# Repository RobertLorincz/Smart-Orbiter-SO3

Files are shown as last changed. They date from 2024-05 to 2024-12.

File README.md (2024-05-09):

# Smart-Orbiter-SO3
This brand new all in one extruder design with many cool features we call Smart Orbiter v3.0  is one of my latest and finest extruder design made in collaboration with LDO Motors. The extrusion system concept and mechanical performances are similar to the Orbiter v2.0 but completely redesigned from scratch.

SO3

**Summary of the coolest features:**

- Pure plated copper heat-block with 72W ceramic heater and Bontech CHT nozzle for highest possible weight VS flow ratio;

- Heat-break performance optimized with finite elements analysis for extreme temperature gradient to ensure clogless free printing experience;

- Unique tensioning mechanism with elastic predefined tension levels

- Frameless recessed 24V fan to reduce the extruder weight and outside dimension

- Large RNC coated dual drive gears with planetary gear reduction, similar to orbiter v2.0

- New precision main shaft design to reduce gear eccentricity

- Full aluminum housing with Delrin plastic gears for low noise and long lifetime

- The smart feature – integrated electronics

- Easy remove system of the secondary drive gear for easy cleaning and maintenance

- Double filament exit guide system for best TPU printing performance

- Overall weight is 175g

**SO3 specifications:**

- Drive type: 12mm dual drive extrusion system

- Weight: 175g including standard hotend

- Nominal steps / mm (16x micro stepping): 690

- Rotation distance: 4.69

- Extrusion force: 6.5Kg+

- Gear ratio: 7.5:1

- Max stepper current: 0.85A RMS (1.2A peak), derating over 50°C ambient temperature.

- Min stepper current: 0.55A RMS (0.75A peak) for operation up to 70°C ambient temperature

- Heater temperature sensor type: ATC Semitec 104NT-4-R025H42G

- Extruder fan: 24V frameless fan with speed signal

- Maximum operating temperature: 90°C (with motor current derating down to 0.55A RMS)

- Filament sensing

- Filament unload

- Hotend lit

- Filament input lit – RGB LED WS2812B type

- Extruder temperature senor: 100K NTC Generic 3950

- Smart features supply: 3.3V or 5V

For more details please visit: https://www.orbiterprojects.com/so3/

Join our support group on Facebook: https://www.facebook.com/groups/705637896767655

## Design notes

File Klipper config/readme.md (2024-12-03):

Changes v2.2.6
- print cancel restores the printer idle timer to 10 min

Changes v2.2.5

- Included CANCEL macro for user using the sensor macros instead of their own macros
- Pausing printer due to runnout detection increases printer timeout to 3600s - 1h (configurable by pause_timeout); timeout set back to default ten minutes after print resume.
- improved temperature restore behavior
- Filament automatic unload after runnout can be disabled by variable disable_runout_unload.
- corrected some minor bugs and spelling
- messages sent to console show SO3: prefix
- corrected RGB led incorrect color status for some failure cases

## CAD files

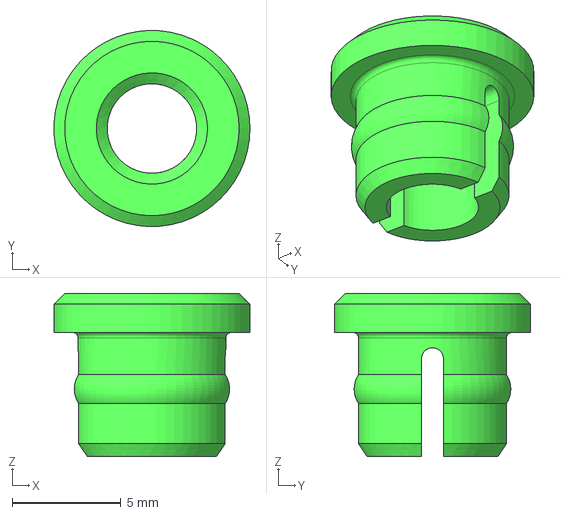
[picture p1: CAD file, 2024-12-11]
3D CAD/SO3_LightRing.step
8.99 x 9.00 x 7.50 mm

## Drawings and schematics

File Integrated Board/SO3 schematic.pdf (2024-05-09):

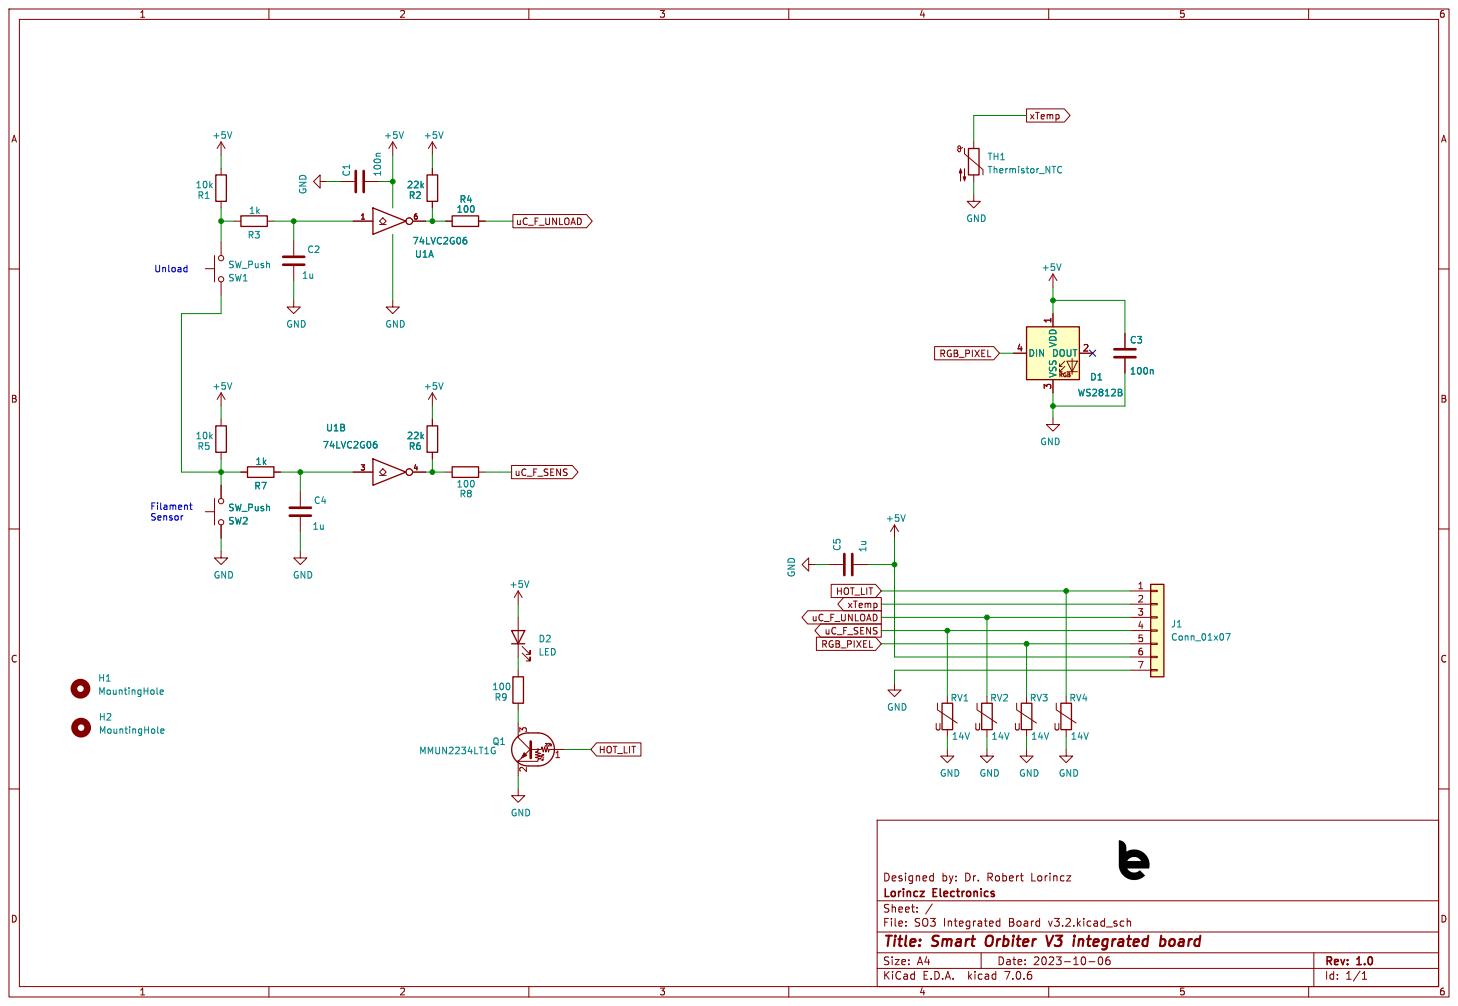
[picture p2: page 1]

Id: 1/1 Title: Smart Orbiter V3 integrated board

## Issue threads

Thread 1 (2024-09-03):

Spare parts?

jjl40, 2024-09-03:
The wires for the hotend cooling fan are too short to reach the tool board and are likely to get pinched. If the wires were 10 mm longer it would be much easier to install. The next problem is finding a replacement.

RobertLorincz, 2024-09-08:
What is the length of your wire, in my case, I had not really issues, but could it be that yours came shorter?

RobertLorincz, 2024-09-08:
For spare parts, you need to ask your local supplier, I insisted a lot on having spare parts also available, but for some reason vendors are not open to it. Its a real issue, I admit, but unfortunately it's hard on my side to change this. It would be better if customers complained directly to the vendors because they can order replacement parts from LDO...but they are not willing to right now. I even asked to at least provide spare parts via AliExpress...so far, still no parts there. Fabreko and Filastruder has some in the US but that is not convenient for everybody.

jjl40, 2024-09-08:
Thank you for your prompt reply Robert,

The hotend fan wire is ~120mm. My mount is a bit unusual due to its layout. I fixed the problem by creating a conduit in the mount so the wire has a direct route to the toolboard. [image0.jpeg]

The only other issue I have is that I have not found a description of how to use the filament load/change. Everything is working fine (the assembly and installation is well documented) but I have not used the automatic loading/change feature.

Cheers

John Lytle

On Sep 8, 2024, at 5:12 AM, LorinczElectronics ***@***.***> wrote:

What is the length of your wire, in my case, I had not really issues, but could it be that yours came shorter?

—
Reply to this email directly, view it on GitHub<https://github.com/RobertLorincz/Smart-Orbiter-SO3/issues/1#issuecomment-2336609975>, or unsubscribe<https://github.com/notifications/unsubscribe-auth/AIE3KPQIGSDHM2OEWTE6K4TZVQIG5AVCNFSM6AAAAABNRGKOSWVHI2DSMVQWIX3LMV43OSLTON2WKQ3PNVWWK3TUHMZDGMZWGYYDSOJXGU>.
You are receiving this because you authored the thread.Message ID: ***@***.***>

jjl40, 2024-09-08:
Thanks again Robert,

I contacted KB3D, where I purchased my Orbiter 3, and Kris informed me that he has the fans in stock. The website was not updated at that time.
This is very convenient for me as KB3D is a short drive for me, just up the road in Twinsburg, Ohio.

Cheers

John Lytle

On Sep 8, 2024, at 5:16 AM, LorinczElectronics ***@***.***> wrote:

For spare parts, you need to ask your local supplier, I insisted a lot on having spare parts also available, but for some reason vendors are not open to it. Its a real issue, I admit, but unfortunately it's hard on my side to change this. It would be better if customers complained directly to the vendors because they can order replacement parts from LDO...but they are not willing to right now. I even asked to at least provide spare parts via AliExpress...so far, still no parts there. Fabreko and Filastruder has some in the US but that is not convenient for everybody.

—
Reply to this email directly, view it on GitHub<https://github.com/RobertLorincz/Smart-Orbiter-SO3/issues/1#issuecomment-2336611208>, or unsubscribe<https://github.com/notifications/unsubscribe-auth/AIE3KPXBTTXBOMIJBFYKJKLZVQIV3AVCNFSM6AAAAABNRGKOSWVHI2DSMVQWIX3LMV43OSLTON2WKQ3PNVWWK3TUHMZDGMZWGYYTCMRQHA>.
You are receiving this because you authored the thread.Message ID: ***@***.***>

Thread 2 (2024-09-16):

revo vs non-revo

mindforger, 2024-09-16:
I have no idea what the difference between the revo and non-revo version is, in the model the only difference seems to be the cableing of the heater, can someone explain? because shop sites also do not state the difference clearly only a 20ish dollar difference

CarVac, 2024-09-23:
Revo versions are for the E3D Revo quick-swap integrated-heatbreak nozzles, not v6 nozzles.

I'd expect that the heatbreak connection is different, the heater is going to be a revo heater of some sort (what wattage?), and there'd be some sort of attachment point for the heater's spring.

mindforger, 2024-09-23:
thank you, i did not visit the site, i was browsing github for extruder options since i wanted to build my own head for my sv08 ... unfortunately i already ruled out the orbiter v3.0 becasue it is too wide to replace the original head and i was unsure if i could use it with the trianglelabs chc pro ... it was a bit confusing to only see the difference in the 3d file

Closed 2024-09-23.

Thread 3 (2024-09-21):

Wire colors in SO3.cfg are backwards

CarVac, 2024-09-21:
I tried to wire my SO3 based on the config file but was getting nonsensical results.

I checked for the thermistor and realized that all the SO3 integrated board wires had backwards colors.

Here's my findings:

```
Orange: ground
White:  5v
Gray:   RGB
Brown:  filament sensor
Yellow: unload button
Red:    temperature
Blue:   hotend light
```

Thus the aliases code should be:

```
  filament_sensor_pin = PC7,         # BROWN signal shall be connected to a digital I/O pin
  filament_unload_pin = PC6,         # YELLOW signal shall be connected to a digital I/O pin
  RGB_pin = PG8,                     # GRAY signal shall be connected to a digital I/O pin
  extruder_temperature_pin = PC1,    # RED signal shall be connected to a temperature sensing input pin
  hotend_lit_pin = PA1,              # BLUE signal shall be connected to a digital I/O pin
```

Also the colors should be documented somewhere else. Maybe on the schematic.

nico9889, 2024-09-21:
I can confirm the issue on the Revo version of the Smart Orbiter, I was convinced the IC board was faulty but after trying @CarVac's color coding I was able to lit the NeoPixel using an Arduino (I still need to test everything else since I need to crimp again all the connectors... and explain to the vendor that the board is probably magically working again and I don't need a replacement anymore 🙈).

@RobertLorincz I'd suggest to create a dedicated page with instructions to setup the Smart Orbiter, I completely missed the reference image under the point "3.3 Integrated Smart Features" in the current page (https://www.orbiterprojects.com/so3/) since it contains **a lot** of mixed information and I didn't expect to find wiring related information under the "Firmware configuration" section.

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

I think the image in the current page is fine, but it need to be put in a more evident place. I wouldn't rely on the cable colors unless there's some kind of warranty that they won't change in the future (I.E: due to a manufacturer decision).

CarVac, 2024-09-21:
Huh, I didn't register that image at all.

Maybe you're right, it probably shouldn't specify wire colors in case it changes.

But I'm glad my findings were able to help someone. Now to wait for my replacement hotend to come in... I had a DOA CHC.

nico9889, 2024-09-21:
I created a pull request to fix the colors specified in the configuration and I added more instruction to wire the Smart Orbiter as well to avoid any possible future mistake. I took the liberty to add you as a co-author since you found both the error and the right wire colors.

RobertLorincz, 2024-09-23:
The problem is that the supplier mixed up the colors and there is not only one variant out there. So I prefer people follows the pin numberings and definition instead of the wire colors.

nico9889, 2024-09-23:
That's exactly what I was worried about. I don't know how familiar you are with GitHub, but I opened a pull request #4 to update the comments in the configuration. I changed the colors according to what CarVac reported and added the pin numbering on the top. Should I remove the colors? Is it fine for you to have the pin numbering inside the configuration? Do you prefer updating the configuration by yourself instead?

If you'll find some time to do that, I'd still strongly suggest to create a dedicated web page with the instruction to setup the Smart Orbiter 3, it's easy to miss the image with the pin numbering on the current page. As a side note I need to make you notice that the website is completely missing information about the Revo version (aside from the small paragraph in the blog post about the SO3), so some people are getting confused #2.

The configuration need to be updated for sure since it's misleading, but about the website it's just a my opinion.

CarVac, 2024-09-23:
I would want to remove all references to colors in the configuration, then, and just have a physical order description in the file.

nico9889, 2024-09-23:
I agree, but I’ll wait for RobertLorincz final decision since this is it’s own project.

Closed 2025-01-16.

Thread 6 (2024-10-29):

E3D PZ Probe

tamebits, 2024-10-29:
Although from the outside it looks as if there was no way to do it, I wanted to double check if there is a way to mount an [E3D PZ Probe](https://e3d-online.com/blogs/news/introducing-pz-probe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) into SO3? This would be an awesome combination.

But it looks like the heat sink is fully integrated into the extruder body.

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

RobertLorincz, 2024-10-30:
In the way this design is done, its not possible to implement it into the SO3...

Tomblarom, 2024-11-29:
I'm using SO3 in combo with a Cartographer3D. I made a neat design, so that it's integrated in the fan and [posted about it here](https://www.facebook.com/groups/705637896767655/posts/1387416425256462).

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

For Cartographer3D there is a new mode called [Survey Touch](https://docs.cartographer3d.com/cartographer-probe/classic-vs-survey-touch). It uses the electrial interference, to detect whether the nozzle touched the bed, functionwise very similar to the E3D PZ Probe. Sure it is not as neatly integrated, but still one of the most precise probes that are available right now.

RobertLorincz, 2024-11-29:
nice design.

tamebits, 2024-11-30:
I’m currently working on a similar solution for beacon probe. I’m still thinking about leaving it in der carrier so I don’t need one for each tool head.

Closed 2024-11-30.

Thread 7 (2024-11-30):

Friction in the upper filament path

tamebits, 2024-11-30:
I just received my SO3. It feels like there is too much friction in the first section. The force required to get the filament moving is somewhere in the range of 7-10 N.
I see something in the filament path. I guess it is some actuator for a micro switch that serves as a filament runout sensor.

Is this amount of friction normal?

RobertLorincz, 2024-12-01:
No, it's not normal; the filament should go in pretty easily. Please take the extruder apart and check if there is not some debris inside the extruder. ALso check the position of the internal electronics board; it could be that the board is not in the correct place and it is closer to the filament than it should be.

tamebits, 2024-12-01:
I took it apart and did not find any debris. I checked the filament diameter and it is 1.75 mm.
The internal board sits flush on the aluminium part. SW2 sits flush on the PCB.
PCB + SW2 fully compressed is 5mm thick. PCB + SW2 released ~ 5.5 mm
The actuator ball is 4 mm.
Anything wrong with that?

The ball left an indent in the switch's button. Looks like the switch is being "over-actuated" which results a lot of friction.

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

RobertLorincz, 2024-12-03:
I can confirm the issue; I'm trying to find out which component is out of spek. It seems there is an issue with some parts causing this issue, I'm in contact with LDO to find and correct the issue. Sure, you will receive replacement parts to fix this.

tamebits, 2024-12-14:
Any update?

tamebits, 2024-12-19:
Thank you Robert,

I asked LDO to get in touch with me. Looks like I have to find another project for the holidays. Or maybe I'll just print a mockup extruder for now ;-)
Merry Christmas and a Happy New Year to you!

tamebits, 2025-01-18:
LDO sent me a replacement part for the upper filament path.

They say the fixed roundness and taper of the ball holes.
Unfortunately that didn't change anything for me. I still have to push with about 8 N.
I guess the steel ball is till over-actuating the microswitch.

msticninja, 2025-01-23:
I just received 4 SO3 Revo Editions, all of them have this problem. It's nearly impossible to push filament in by hand. Also, there were two mounting holes that weren't even drilled and tapped on one of them. What's going on with manufacturing?

RobertLorincz, 2025-02-03:
I ask LDO to look into this issue. its OK to have slight friction, but it should go in easily.

RobertLorincz, 2025-02-03:
Would it be possible to send me pictures with the sensor switch position? Maybe is not flush with the PCB and there is a gap between the sensor swicth and the PCB?

tamebits, 2025-02-18:
Sorry for the late resposne, I was too busy with other things.

The button is slightly rotated, but it sits flush with the board. The board is 1.2 mm thick.
PCB plus released button is 5.5 mm
PCB plus fully pressed button is 5 mm

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

The PCB barely sits flush on the CNC part.

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

I think the switch is too close to the filament path.

Rico-origin, 2025-03-24:
I received my SO3 on the 14.3.2025, and this problem still persists. I purchased it from 3DJake in Europe. Is there a solution for this?
As my printer still uses Marlin 2 firmware, and there is no Marlin 2 configuration for this extruder and my printer combo, I am not using any smart features for now, so I just dissasembled the extruder and removed the ball, which actuates the switch.
My switch doesn't have an indent from the ball as on the picture above.
Please let me now what is the fix and if I need do contact the distributor. Maybe slightly smalled diameter ball for switch actuation?

tamebits, 2025-03-24:
As I didn't hear form LDO in a while so I decided to fix the problem myself.

I carefully reduced the button's height until the friction felt ok. After that I checked that the steel ball still actuates the button.

I'm sure you can also increase the diameter of the filament bore but I figured replacing the SMD button would be easier than replacing the CNC part in case I mess things up.

tamebits, 2025-03-24:
>  Maybe slightly smaller diameter ball for switch actuation?

I only had 3.5 mm around which is already too small to actuate the button

If you find balls in 0.1 or even 0.05 mm increments you could test which one is good for you.
It probably doesn't take much to get rid of the friction.

RobertLorincz, 2025-03-24:
Thanks for the feedback, I will ask again LDO guys to double check this before shipping. The filament should go inside relatively easily. It's not OK to have high friction in there. One easy way to recuce this would be to use a smaller steel ball or try to cut a little down from the top of the button with a sharp cutter knife.

MerlinBaumann, 2025-04-30:
Hi
While my extruder was fine at first, the friction issue appeared after around 50h-100h of printing the first time. When the tensioning lever is removed, I saw that the main drive gear was displaced axially to the front (fan). After realigning the teeth for the filament with the bore, the extrusion was good again. After some more printing hours the flow rate of PETG with a CHT 0.4mm nozzle decreased from more than 18mm3/s to less than 10mm3/s before the extruder starts to skip steps.
Filament changes need a lot of force, too.

Removing the tension lever again, shows that the main drive gear moved axially to the back this time.
(The set screw was in place and tight during operation)

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

The scratched off anodization at the top of the upper edges of the filament guide idicates, that the filamet did rub against the guide. Sometimes scratch maks chould be seen on the side of the filament, too.

The secondary dive gear is axailly floating on the bearing in the lever only guided by the filament.
Thus the axial displacement of the main drive gear results in the same displacement of the secondary drive gear.
The picture below shows scratched anodization on the lever on the left side. This further increases friction as aluminum is not a metal that slides well.

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

I have no explanation for the scratches in the middle of the gear.
Maybe the indents of the screw on the pivot point of the lever change the geometry to allow for contact with the filament guide. Maybe not. I didn't measure the details in the CAD model. Maybe it was some debris at some point.

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

However, it seems to me that main drive gear can shift axially on its shaft, which leads to friction in multiple places. Is there a way to constrain axial movement of the main drive gear on the shaft? The set screw and pressure fit don't seem to provide sufficient force to do so.
Could the sum of all tolerances over the shaft and housing parts result in to much axial clearance for some units while others good?

What do you think?

msticninja, 2025-07-01:
I removed .55mm from the tops of the switches to get reliable triggering with very little friction. Be careful with this route, as taking off too much will cause unpredictable/incorrect runout alarms to trigger.

b-A-shi, 2025-07-03:
That felt very wrong, but I managed to solve it.
Instead of cutting the button, I used a fine sanding paper to lower the button

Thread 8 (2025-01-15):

not an issue, a question!!! voltage for the ceramic heater?

klayus, 2025-01-15:
I can't find anywhere what is the voltage for the ceramic heater. I assume is 24V as that what is required for the fan, but thought I ask first.

RobertLorincz, 2025-01-16:
The Orbiter 3 is designed for 24V only, same for the heater voltage.

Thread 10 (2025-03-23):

Tensioner lever resetting itself from L1 to open on filament load

zipzapchap, 2025-03-23:
Title. I loaded filament, and as it went through the macro, the tensioner lever clicked from L1 to open. It also refuses to move to L1 with filament loaded, but can stick at L2, which is obviously not ideal for PLA. I have the toolboard and the SO3, and I have followed (roughly) the guide found [here](https://www.printables.com/model/1094931-smart-orbiter-v30-tool-head-for-ender-3-v2-with-de) to install it on my ender 3 v2.

zipzapchap, 2025-03-23:
WELP. That's entirely my bad... Looks like I need to do some more research on filament tensioning. L1 is for SOFT filaments, L2 is for HARD. Sorry for the user-error-induced issue!

Closed 2025-03-23.

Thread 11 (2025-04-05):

Cooling fan noise

dpellegr, 2025-04-05:
Hi,

I was wondering if anybody has a solution to reduce the fan noise. It produces a quite high pitch whistle doesn't seem much at first, but after few hours in the same room makes me go crazy.

I modded my old extruder with an ultra silent Noctua fan, but here the fan is somehow integrated and the noise likely comes from the fan blades passing in front of the fins. I feel that a more traditional heatsink design with plenty of fins and a slow spinning fan sitting on the top, would be much more silent and effective, albeit less compact. I am evaluating this route, but I would need cut away the existing fins and I would happily go for a solution that does no require machining.

Any idea?

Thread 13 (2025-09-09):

Load cell support

johnboiles, 2025-09-09:
My compliments on this extrusion system. It seems like the most elegant one out there!

In my opinion, the only thing holding it back from being absolutely perfect is load cell sensor support. Load cell has emerged for the higher end consumer printers (e.g. Bambu Lab, Prusa) as the most common way of doing mesh leveling.

I'm wondering @RobertLorincz if you've put any thought into this. I suppose one option would be to mount the extruder on a load cell. Another option could be to integrate the load cell sensor in the heatbed (like Bambu Lab does). If there's a best way to do this that you've seen, or if you have any ideas, I'm all ears!

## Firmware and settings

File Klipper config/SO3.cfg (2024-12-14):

############################################################################
############################ SmartOrbiter v3 ###############################
############################################################################

#config file version v2.2.7
#release date: 14.12.2024

#Contributors: Lorincz Robert, Tomblarom

# PAUSE, RESUME and CANCEL macros are defined at the end of this config file.
# If you prefer using your own please delete them, otherwise define parking position below.
#when using PAUSE, RESUME and CANCEL macros of this file, please comment out the #[inlcude mainsail.cfg] from you printer.cfg file.

[board_pins SMARTORBITER3] 
aliases: ### define here the pins to which the SO board is connected #######
  filament_sensor_pin = PC7,         # SO3 Pin4 signal shall be connected to a digital I/O pin
  filament_unload_pin = PC6,         # SO3 Pin3 signal shall be connected to a digital I/O pin
  RGB_pin = PG8,                     # SO3 Pin5 signal shall be connected to a digital I/O pin
  extruder_temperature_pin = PC1,    # SO3 Pin2 signal shall be connected to a temperature sensing input pin with 4.7K pull up resistor
  hotend_lit_pin = PA1,              # SO3 Pin1 signal shall be connected to a digital I/O pin
  ex_step_pin = PC12,                # Extruder STEP signal to be connected to digital IO pin
  ex_dir_pin = PD1,                  # Extruder DIR signal to be connected to digital IO pin
  ex_en_pin = PD2,                   # Extruder Enable signal to be connected to digital IO pin
  ex_uart_pin = PD0,                 # Extruder stepper dirver UART communication pin / comment section out for stand alone stepper drivers
  ex_heater_pin = PG12,              # Extruder heater pin, to he connected to a heater output   
  ex_fan_pin = PE2,                  # Extruder fan speed control pin
  ex_fan_tacho = PE3,                # Extruder fan tacho signal, delete line if not used
  ex_tsensor_pin = PC0               # Hotend temperature sensor input pun, to be connected to temperature sensing input


#################################################################################################################
################################ CHANGE HERE MACRO CONFIGURABLES ################################################
#################################################################################################################

[gcode_macro _SENSOR_VARIABLES]         # change here macro configurables, enable disable functions!*************************
variable_filament_load_temp     :230    # temperature to heat up hotend for filament loading, default is 235
variable_filament_unload_temp   :185    # temperature to heat up hotend for filament un-loading, default is 185
variable_filament_load_min_temp :190    # minimum hotend set temperature allowed in filament load macro, default is 190
variable_nozzle_purge_length    :70    # filament extrude amount during load sequence, hotend purge from old filament, default is 100
variable_nozzle_purge_speed     :300    # filament extrude speed in mm/min adjust this value lower if flow is too high and extruder skips during loading, default is 300
variable_temp_restore           :True   # [True] restore previous temperature after filament change
variable_disable_autoload       :False  # disable filament autoload feature by setting this variable True
variable_disable_runout         :False  # disable runout by setting this variable True
variable_disable_autounload     :False  # disable auto unload filament by setting this variable to True
variable_pause_on_unload_button :True   # pauses the printer if the unload button is pressed during printing
variable_disable_runout_unload  :True   # disable auto filament unload after runout detection
variable_pause_timeout          :3600   # printer timeout setting in seconds, avoids disabling of steppers and heaters after klipper default timeout of 600s 
variable_enable_beep            :True   # uses M300 sound feature, set it True to enable																					  
variable_park_position_x        :100    # set your X parking position here for pause macro trigerred by runout
variable_park_position_y        :-5     # set your Y parking position here for pause macro trigerred by runout
variable_park_lift_z            :10     # set your Z lift amount for parking position here, default is 10
variable_park_retraction        :1      # set your retraction amount for parking, default is 1
gcode:

[force_move]
enable_force_move: True

[respond]
default_type: echo
  
##################################################################
########################## EXTRUDER ##############################
##################################################################
[extruder]
step_pin: ex_step_pin
dir_pin: ex_dir_pin
enable_pin: !ex_en_pin
microsteps: 32
full_steps_per_rotation: 200
#rotation_distance = <full_steps_per_rotation> * <microsteps> / <steps_per_mm>
rotation_distance: 4.69
nozzle_diameter: 0.400
filament_diameter: 1.750
max_extrude_only_distance: 2500
max_extrude_only_velocity: 120
max_extrude_only_accel: 3000
#_______________________ HEATER NOZZLE ____________________________
sensor_pin: ex_tsensor_pin
heater_pin: ex_heater_pin
#_________________________NOZZLE TEMP _____________________________
sensor_type: ATC Semitec 104NT-4-R025H42G  
pullup_resistor: 4700
min_temp: 0
max_temp: 300
pressure_advance: 0.015
pressure_advance_smooth_time: 0.03
min_extrude_temp: 170
smooth_time: 0.5
max_extrude_cross_section:10
max_power: 0.995
pwm_cycle_time: 0.01
control = pid
pid_Kp=24.859 
pid_Ki=2.072 
pid_Kd=74.578

[tmc2209 extruder] 
uart_pin: ex_uart_pin
uart_address: 3 # comment out this line in case UART address definition is not required
interpolate: true
run_current: 0.8
sense_resistor: 0.11
stealthchop_threshold: 0

[heater_fan extruder_Fan]
pin: !ex_fan_pin
tachometer_pin: ex_fan_tacho
tachometer_ppr: 2
tachometer_poll_interval: 0.0005
heater: extruder
cycle_time: 0.0001 #10KHz PWM frecvency, do not change this
heater_temp: 85
fan_speed: 0.65 # increase in case experiencing clogging during printing.
hardware_pwm: false
shutdown_speed: 0.0
max_power: 1.0

[firmware_retraction]
retract_length: 1.0
retract_speed: 100
unretract_extra_length: 0.0
unretract_speed: 80

#################################################################################################################################
########################################### SO3 Features Configuration ##########################################################
#################################################################################################################################

[output_pin hot_lit]
pin: hotend_lit_pin
pwm: False
value: 1

[neopixel SO3RGB]
pin: RGB_pin
chain_count: 1
color_order: GRB
initial_RED: 0.0
initial_GREEN: 1.0
initial_BLUE: 0.0

[thermistor SO3Thermistor]
temperature1: 25
resistance1: 100000
beta: 3950

[temperature_sensor SO3]
sensor_type: SO3Thermistor
sensor_pin: extruder_temperature_pin
pullup_resistor: 4700
min_temp: 0
max_temp: 85

#################################################################################################################################
############################################## Runout and autoload macros #######################################################
#################################################################################################################################

#################################################################################################################################
####################################### DO NOT CHANGE ANYTHING BELOW THIS LINE!!! ###############################################
#################################################################################################################################
####################################### UNLESS YOU KNOW WHAT YOU ARE DOING OR YOU ARE BORED AND NEED TO DO SOMETHING OR YOU ARE ALONE AND NEED SOMETHING TO MESS UP YOUR LIFE OR YOU CAN DO IT BETTER THAN ME OR YOU ARE A REAL SMARTASS OR JUST BECAUSE YOU CAN OR YOU RUN OUT OF BEAR OR HAS NOTHING BETTER TO DO OR ANY UNREASONABLE REASON
#################################################################################################################################


#*****************************initial RGN LED set at printer start****************************************************************
[delayed_gcode startup_RGB_SET]
initial_duration: 2
gcode:
  {% if printer["filament_switch_sensor SO3Sensor"].filament_detected==true %}
      SET_LED LED=SO3RGB RED=0.0 GREEN=1.0 BLUE=0.0
  {% else %}
      SET_LED LED=SO3RGB RED=1.0 GREEN=0.0 BLUE=0.0
  {% endif %}


#***********************************filament switch definition***********************************************************
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
